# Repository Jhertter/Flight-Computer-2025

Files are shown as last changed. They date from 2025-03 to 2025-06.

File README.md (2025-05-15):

# ITBA Rocketry Team - Avionics&recovery
Documentation of SRAD Flight Computer

---

## Description

- Hardware design and implementation of the 2025 on board flight computer.
- Software used to capture data and transmit it to the ground station.

## FC implementation diagram

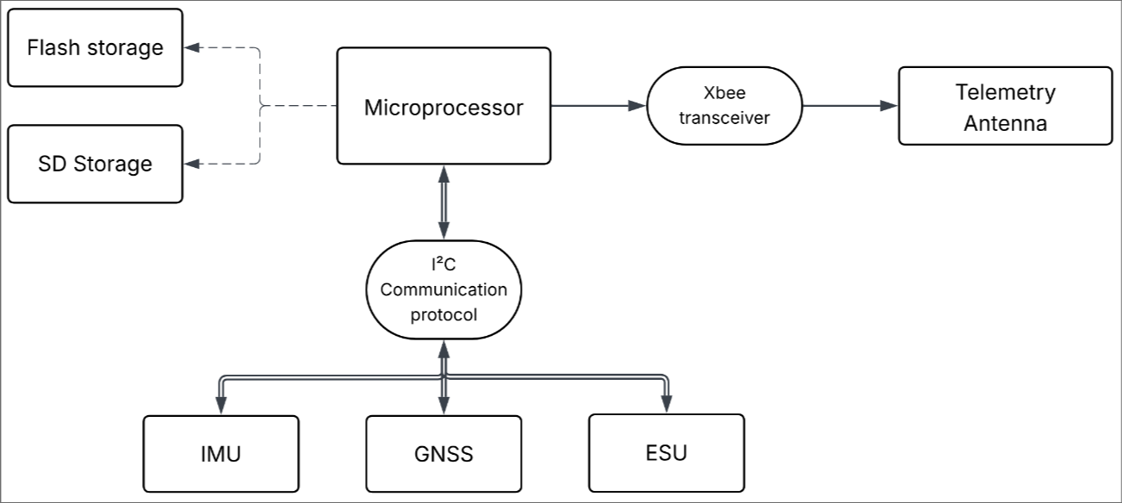
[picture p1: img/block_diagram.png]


## Authors

José Ivan Hertter
Ezequiel Diaz Guzmán

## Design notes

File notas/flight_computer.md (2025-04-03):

# ITBA Rocketry - A&Rocketry
## Flight Computer

### <u>Edición 2025</u>

Si llega a haber freno de aire, va a tener una cpu distinta

La placa SRAD tranquilamente puede ser de 90x150mm (el 90 está muy justo, el otro se puede ajustar). Si la tenemos lista para finales de febrero podriamos mandar a fabricarla.

Tener BOM para 28/01. Armar un GANT con final el 10/04

### Minutas reuniones

#### 10/03

2 compu/altimetros ccomercciales (RRC3 ni idea) 

ver si podemos activar la SRAD FC a mas de 2km o ver si se puede mantener prendido 10hs. Cambiaron el sensor de presion y temperatura

MPU 9050

puertos
RP4020 x3
flash x2
M8Q x1
bateria holder
18450  x4

Consideraciones de la placa
- dejar marcas de tornillos y bulones
- equilibrar la placa
- 90x120mm, puede ser hasta 150mm
- no poner todo de un lado y dejar el resto vacio
  
Investigar un poco sobre la placa para BMS

#### 27/03

- ~~usar shielding de GND para nets sensibles (SAM + flash)~~
- ver alternativas de capacitores para no usar 7 para la rpi -> miguel o pañol
- poner leds (pueden ser smd, mejor de colores distintos)
- ~~si es doble capa se puede usar nets como caps para VCC~~
- ~~conexión a xbee~~
- ~~poner opción de conectar una bornera y que un PMOS haga de llave driveado por el micro (camara), usa latch~~?
- ~~el MPU viene con placa integrada, es mejor sacarlo o dejarlo y conectar eso?~~
- poner pulsador por las dudas (ej: al tocar se envia la mem por el usb)
- no usar plano de masa general del otro lado (acople)
- ~~asegurarse que los caps de desacople esten antes de las entradas~~
- no exponer el BME280 a mucha luz (es fotosensible)
- a~~l gps va a haber que aisalrlo en la placa, dejarlo en una esquina separado y tiene que estar en un plano de GND de 50x50 mm ~~
- ~~ver SAM-M8Q Hardware Integration Manual, UBX-16018358 pag 12~~
- ~~usar conexión troncal para VCC y GND, dejar al final el gps~~
- va a haber que hacerle un case con tapa a la placa para evitar corrientes de aire
- usar pulsera antiestática
- a nivel bahía analizar la posición para maximizar el diagrama de radiación
- el regulador lo pondría arriba del usb, sería reg-usbc-jumper-bornera3

### Componentes

#### Micro
-   RP2040
    -   Cores: 2
    -   Clk: 133MHz
    -   GPIO: 34
    -   DAC: nada
    -   ADC: 4 canales, 12-bits
    -   Protocolos: UART, SPI, I2C, I2S, PIO    
    -   Consumo: es menor que el de Xtensa LX6
    -   Precio: ~$1000
    -   Comentarios: Como no vamos a usar los módulos wifi y bluetooth (las telemetrías se van a hacer por algún módulo LoRa), va a ser mejor usar el rp2040 para poder controlar mejor los modulos. Xtensa LX6 tiene limitaciones para operaciones en tiempo real (medio que ya lo vimos para el final de labo3). El RP2040 dicen que está diseñado especificamente para operaciones de baja latencia.
    -   PIO block: modulo para operaciones I/O de hasta 133MHz (en la esp llega a 40MHz masomenos)

#### Periféricos
- <u>Memoria:</u>
    - W25Q80DV:
        - Protocolo com: SPI
        - Precio: $477
-   <u>Sensor de presión:</u>
    -   BMP390. Podría usarse además un altimetro GPS para más precisión.
-   <u>GPS altimetro:</u>  
    -   GP-02
        -   Protocolo com: UART
        -   GNSS: BDS, GPS, GLONASS
        -   Precision: <2m
        -   Alimentacon: 3.3V
        -   Precio: $9600 + envio
    -   GlobalTop FGPMMOPA6H
    -   SparkFun GPS-RTK-SMA (ZED-F9P)
    -   u-blox NEO 8M:
        -   Protocolo com: UART, I²C, SPI
        -   GNSS: GPS, Galileo, BeiDou, GLONASS
        -   Precision: 1cm (RTK)
        -   Alimentación: 3.3V
        -   Precio: U$D 129
    -   Adafruit Ultimate GPS Module (MTK3339)
        -   Protocolo com: UART
- <u>Sensor de temperatura:</u>
    - HS3001: 
      - Protocolo com: I²C
      - Alimentación: 2.3V a 5.5V
      - Precisión: 0.25ºC
      - Rango: -10 a 80ºC
      - Precio: $3095
    - MAX31865
      - Protocolo com: 
      - Alimentación:
      - Precisión:
      - Rango: 
      - Precio: 
    - HTU21D      
      - Protocolo com: 
      - Alimentación:
      - Precisión:
      - Rango: 
      - Precio:
- <u>Acelerómetro y giroscopio:</u>
  - MPU6050:
      - Protocolo com:
      - Alimentación:
- <u>GPS:</u>

cargas pitorecnicas (despliegue nose cone y paracaidas)

### <u>Edición 2024</u>
#### Micro
-   ESP32 (Xtensa LX6):
    -   Cores: 2
    -   Clk: 240MHz
    -   GPIO: 34
    -   DAC: 2 canales, 8-bit
    -   ADC: 18 canales, 12-bits
    -   Protocolos: UART, SPI, I2C, I2S, CAN
    -   Precio: 
#### Perifericos
-   <u>Sensor de presión:</u> BMP390.
    -   Protocolo de com: I²C y SPI
    -   Precio unitario:
    -   Para medir altitud. Cons. Requiere calibración con la presión atmosférica del lugar y es muy sensible a cambios climaticos.
-   <u>Memoria:</u> W25Q80DV. 
    -   Serial flash memory. 
    -   Protocolo de com: SPI.
    -   Precio unitario: 
-   <u>Acelerometro:</u> MPU-6050. 
    -   Protocolo de com: I²C. *
    -   Precio unitario:
    -   Tiene giroscopio. 
-   <u>Pyro channels:</u>   
-   <u>Regulador de tensión:</u>
    -   Precio unitario: *

### 2023

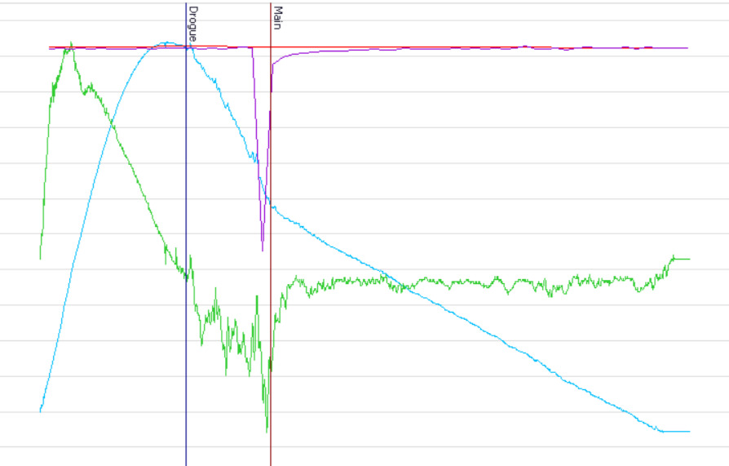
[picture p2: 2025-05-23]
2024_lanin_data/croped.jpg

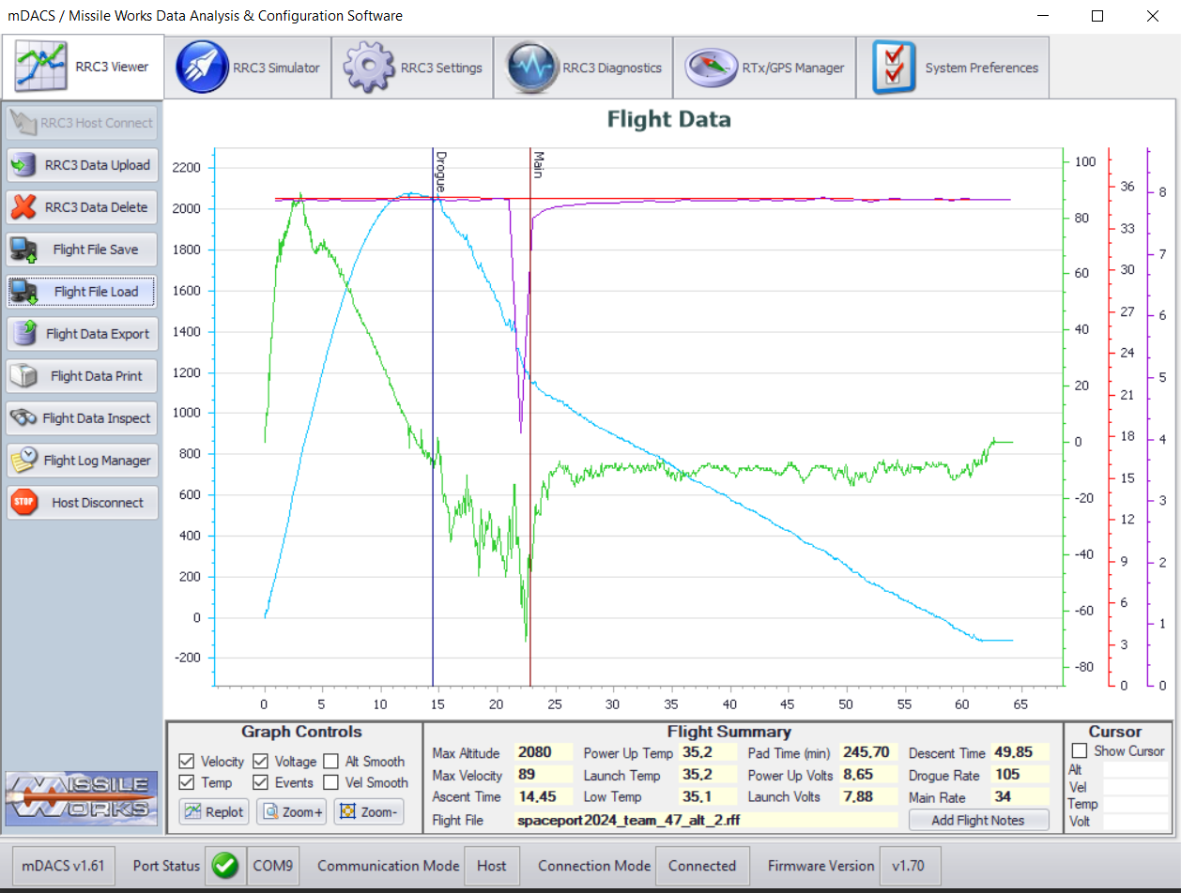
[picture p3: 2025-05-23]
2024_lanin_data/spaceport2024_team_47_alt_2.png

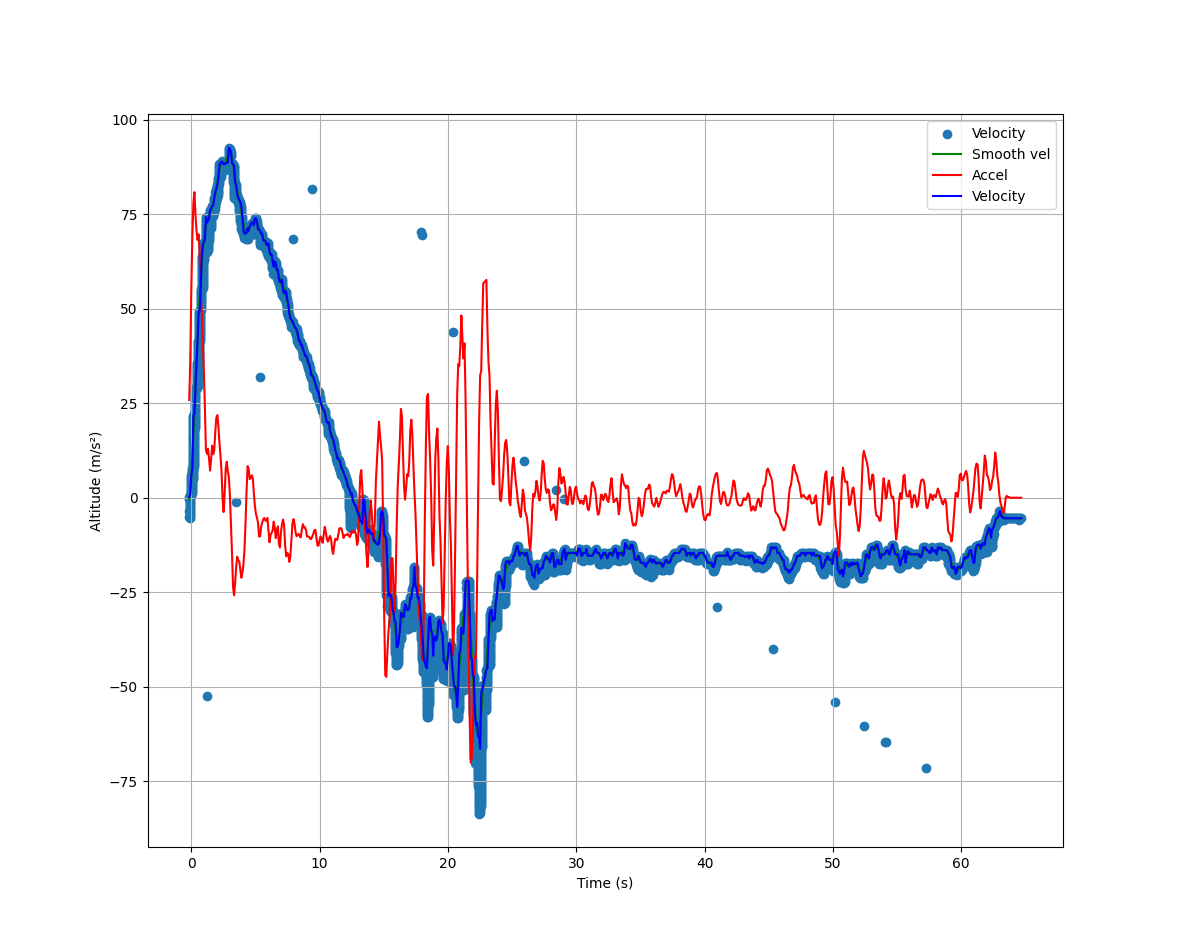
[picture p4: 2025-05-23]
2024_lanin_data/full_mission.png

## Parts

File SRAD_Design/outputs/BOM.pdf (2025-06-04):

BOM

Id Designator
14 U1
20 U2
6 J7
30 U3
17 R9
4 R2
15 R3,R4
26 R1,R5
5 R15,R16,R14
8 R13,R12
10 R_BME_SDA1,R_BME_SCL1,R_SAM_SDA1,R_MPU_SCL1,R_MPU_SDA1,R_SAM_SCL1 13 R_BL2
21 R10,R11
22 R_BL1
19 S2,S3,S1
28 U4
12 J5
18 J1
25 U5
32 U6
1 D2,D1,D3
9 Y1
3 C8,C10
7 C1,C4,C17
24 C6,C14,C13,C15,C7,C11,C12,C9,C5,C16
29 C2,C3
2 C_BME_VDDIO1,C_VDD_MPU1,C_MPU_REG1,C_BME_VDD1 11 C_VDDIO_MPU1
16 C_SAM_VCCIO1,C_SAM_VCC1,C_SAM_VBCKP1
23 C18
27 J4
31 J2

Footprint | Quantity Designation
SOT-223-3_TabPin2 | 1 NCP1117-3.3_SOT223
SOIC-8_5.3x5.3mm_P1.27mm | 1 W25Q128JVS
SAMESKY_UJ20-C-H-G-SMT-6-P16-TR | 1 UJ20-C-H-G-SMT-6-P16-TR
RP2040-QFN-56 | 1 RP2040
R_0805_2012Metric_Pad1.20x1.40mm_HandSolder | 1 | 150
R_0805_2012Metric | 1 DNF
R_0805_2012Metric | 2 | 27
R_0805_2012Metric | 2 1k
R_0805 | 3 10k
R_0805 | 2 R
R_0805 | 6 2k7
R_0805 | 1 8k2
R_0805 | 2 | 150
R_0805 | 1 15k
PTS810SJK250SMTRLFS | 3 PTS810SJK250SMTR_LFS
PSON65P250X250X100-8N | 1 BME280
PinHeader_1x03_P2.54mm_Vertical | 1 Connector_3_Pol
PinHeader_1x02_P2.54mm_Vertical | 1 Connector_2_Pol
MPU-9250 | 1 MPU-9250
MODULE_SAM-M8Q-0-10 | 1 SAM-M8Q-0-10
LED_0805_2012Metric_Pad1.15x1.40mm_HandSolder | 3 LED
Crystal_HC49-4H_Vertical | 1 Crystal
C_0805_2012Metric | 2 1u
C_0805_2012Metric | 3 10u
C_0805_2012Metric | 10 100n
C_0805_2012Metric | 2 15p
C_0805 | 4 100n
C_0805 | 1 10n
C_0805 | 3 C
C_0805 | 1 10u
Bornera_2_P5mm | 1 Terminal_2
693071010811 | 1 503398-1892

Supplier and ref

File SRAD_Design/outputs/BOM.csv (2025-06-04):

Id | Designator | Footprint | Quantity | Designation | Supplier and ref
1 | D2,D1,D3 | LED_0805_2012Metric_Pad1.15x1.40mm_HandSolder | 3 | LED
2 | C_BME_VDDIO1,C_VDD_MPU1,C_MPU_REG1,C_BME_VDD1 | C_0805 | 4 | 100n
3 | C8,C10 | C_0805_2012Metric | 2 | 1u
4 | R2 | R_0805_2012Metric | 1 | DNF
5 | R15,R16,R14 | R_0805 | 3 | 10k
6 | J7 | SAMESKY_UJ20-C-H-G-SMT-6-P16-TR | 1 | UJ20-C-H-G-SMT-6-P16-TR
7 | C1,C4,C17 | C_0805_2012Metric | 3 | 10u
8 | R13,R12 | R_0805 | 2 | R
9 | Y1 | Crystal_HC49-4H_Vertical | 1 | Crystal
10 | R_BME_SDA1,R_BME_SCL1,R_SAM_SDA1,R_MPU_SCL1,R_MPU_SDA1,R_SAM_SCL1 | R_0805 | 6 | 2k7
11 | C_VDDIO_MPU1 | C_0805 | 1 | 10n
12 | J5 | PinHeader_1x03_P2.54mm_Vertical | 1 | Connector_3_Pol
13 | R_BL2 | R_0805 | 1 | 8k2
14 | U1 | SOT-223-3_TabPin2 | 1 | NCP1117-3.3_SOT223
15 | R3,R4 | R_0805_2012Metric | 2 | 27
16 | C_SAM_VCCIO1,C_SAM_VCC1,C_SAM_VBCKP1 | C_0805 | 3 | C
17 | R9 | R_0805_2012Metric_Pad1.20x1.40mm_HandSolder | 1 | 150
18 | J1 | PinHeader_1x02_P2.54mm_Vertical | 1 | Connector_2_Pol
19 | S2,S3,S1 | PTS810SJK250SMTRLFS | 3 | PTS810SJK250SMTR_LFS
20 | U2 | SOIC-8_5.3x5.3mm_P1.27mm | 1 | W25Q128JVS
21 | R10,R11 | R_0805 | 2 | 150
22 | R_BL1 | R_0805 | 1 | 15k
23 | C18 | C_0805 | 1 | 10u
24 | C6,C14,C13,C15,C7,C11,C12,C9,C5,C16 | C_0805_2012Metric | 10 | 100n
25 | U5 | MPU-9250 | 1 | MPU-9250
26 | R1,R5 | R_0805_2012Metric | 2 | 1k
27 | J4 | Bornera_2_P5mm | 1 | Terminal_2
28 | U4 | PSON65P250X250X100-8N | 1 | BME280
29 | C2,C3 | C_0805_2012Metric | 2 | 15p
30 | U3 | RP2040-QFN-56 | 1 | RP2040
31 | J2 | 693071010811 | 1 | 503398-1892
32 | U6 | MODULE_SAM-M8Q-0-10 | 1 | SAM-M8Q-0-10

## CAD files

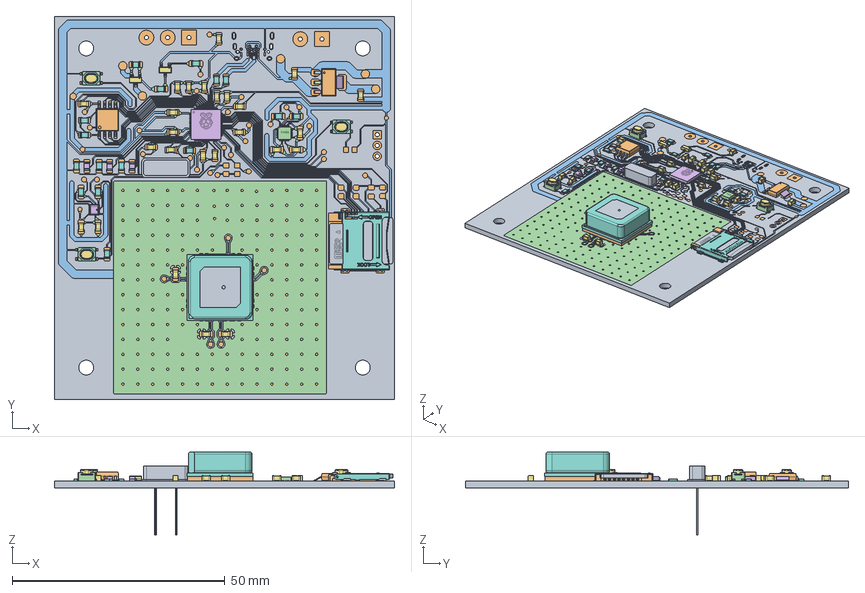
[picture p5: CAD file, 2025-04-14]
SRAD_Design/SRAD_computer.FCStd
80.0 x 90.0 x 19.5 mm
Pcb_98ea
topPads_98ea
topTracks_98ea
topZones_98ea
botPads_98ea
D2_LED_0805_2012Metric_d771bca645d1 x 3
C_BME_VDDIO1_C_0805_2012Metric_c2abb37d300b x 25
R7_R_0805_2012Metric_f4d0965d4664 x 16
Y1_ECS-120-20-4_43d50dad4b6c
PinsArrayL
PinsArrayL001
PinsArrayL002
FilletPinR
PinsArrayL004 x 2
PinsArrayL005 x 2
FilletPinR001 x 2
PTS810SJK250SMTR LFS x 3
PTS810SJK250SMTR LFS001 x 3
PTS810SJK250SMTR LFS002 x 3
PTS810SJK250SMTR LFS003 x 3
PTS810SJK250SMTR LFS004 x 3
PTS810SJK250SMTR LFS005 x 3
PTS810SJK250SMTR LFS006 x 3
MICRO SD CARD
PinsArrayLR
PinsArrayLR001
PinsArrayLR002
PinsArrayLR003
PinsArrayLR004
PinsArrayLR005
PinsArrayLR006
PinsArrayLR007
ICM-20948
ICM-20949
ICM-20950
ICM-20951
ICM-20952
ICM-20953
ICM-20954
ICM-20955
ICM-20956
ICM-20957
ICM-20958
ICM-20959
ICM-20960
ICM-20961
ICM-20962
ICM-20963
ICM-20964
ICM-20965
ICM-20966
ICM-20967
ICM-20968
ICM-20969
ICM-20970
ICM-20971
ICM-20972
ICM-20973
BME280
BME281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

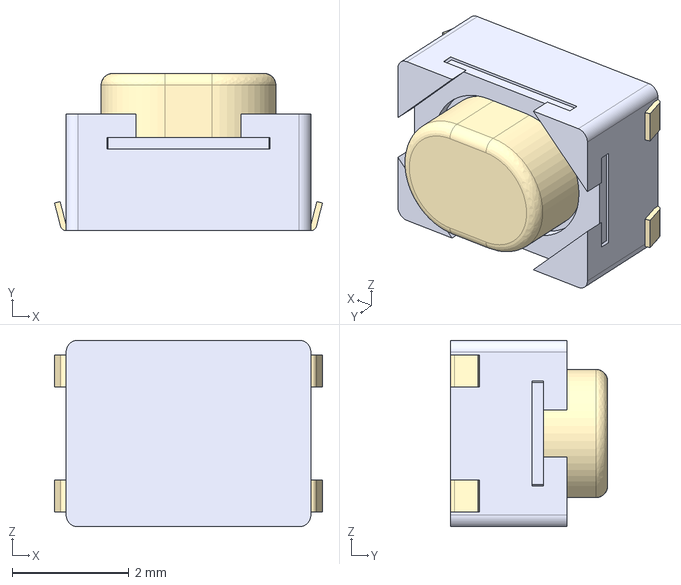
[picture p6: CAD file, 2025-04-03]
SRAD_Design/3dmodels/PTS810SJK250SMTR_LFS.step
4.60 x 2.70 x 3.20 mm

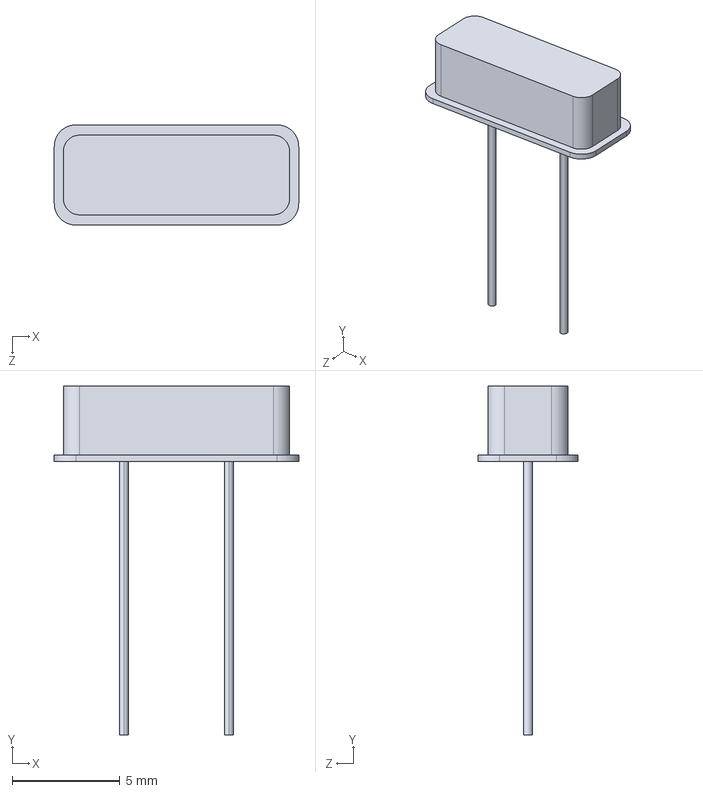
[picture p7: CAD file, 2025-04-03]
SRAD_Design/3dmodels/Crystal_HC49-4H.step
11.3 x 16.2 x 4.65 mm

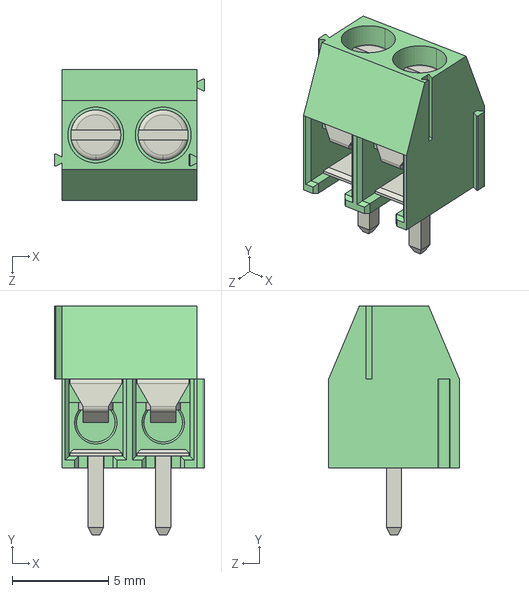
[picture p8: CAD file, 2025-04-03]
SRAD_Design/3dmodels/Terminal_Block_2.step
7.80 x 11.9 x 6.80 mm

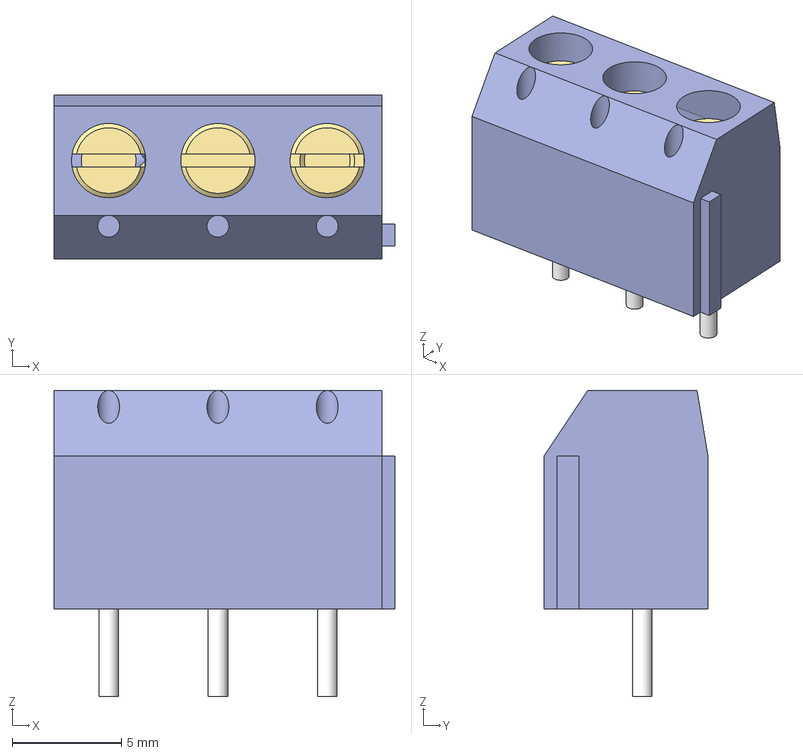
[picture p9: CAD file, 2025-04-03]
SRAD_Design/3dmodels/Terminal_Block_3.step
15.6 x 7.50 x 14.0 mm

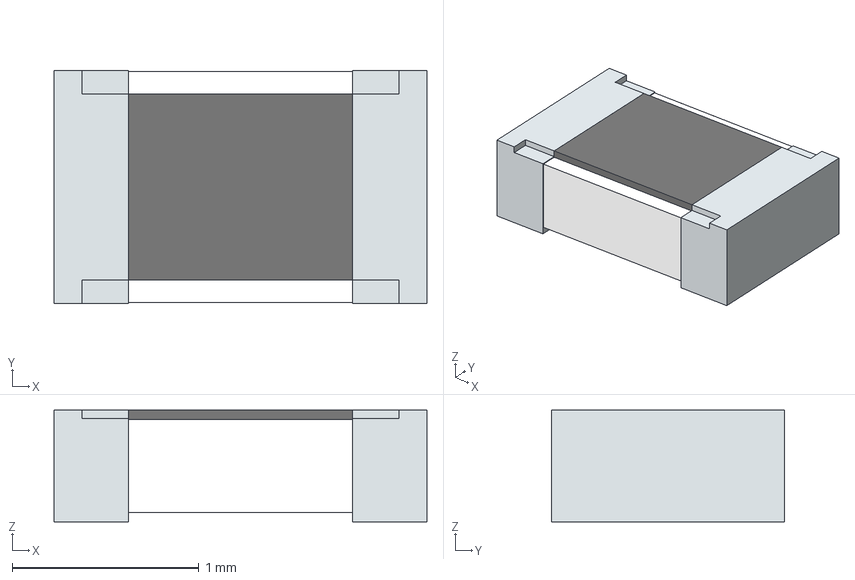
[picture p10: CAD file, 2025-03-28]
SRAD_Design/3dmodels/0805_res.step
2.00 x 1.25 x 0.6 mm
solidBody
Terminal
solidTop

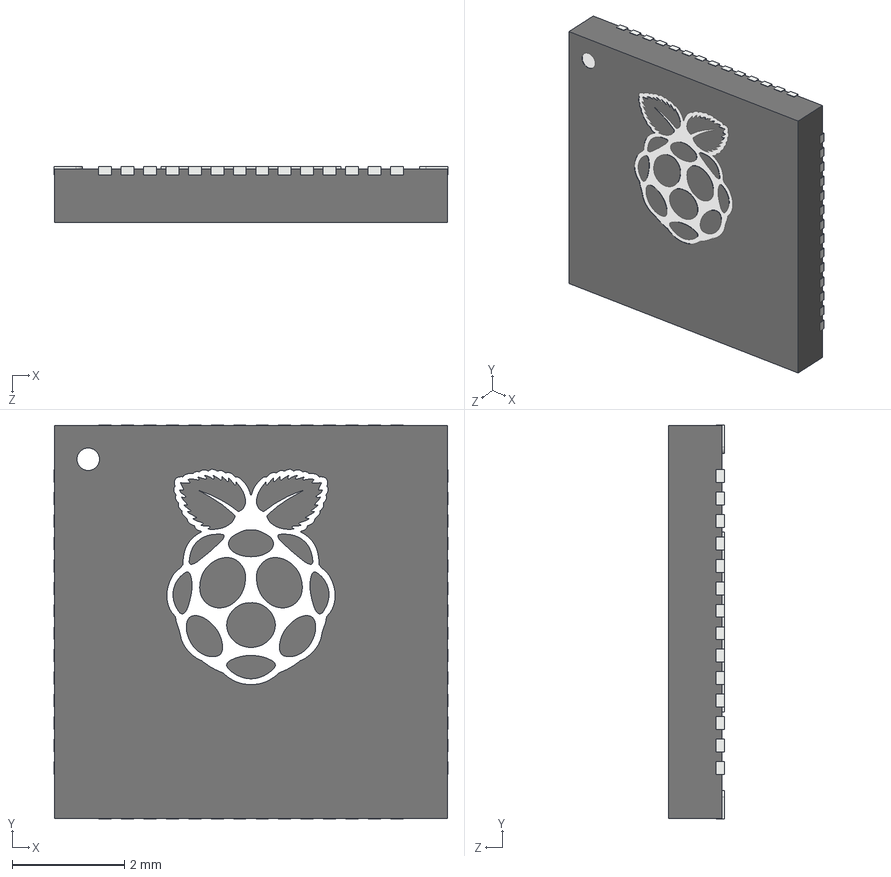
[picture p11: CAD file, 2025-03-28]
SRAD_Design/3dmodels/RP2040_QFN_PACKAGE.STEP
7.02 x 7.02 x 1.00 mm

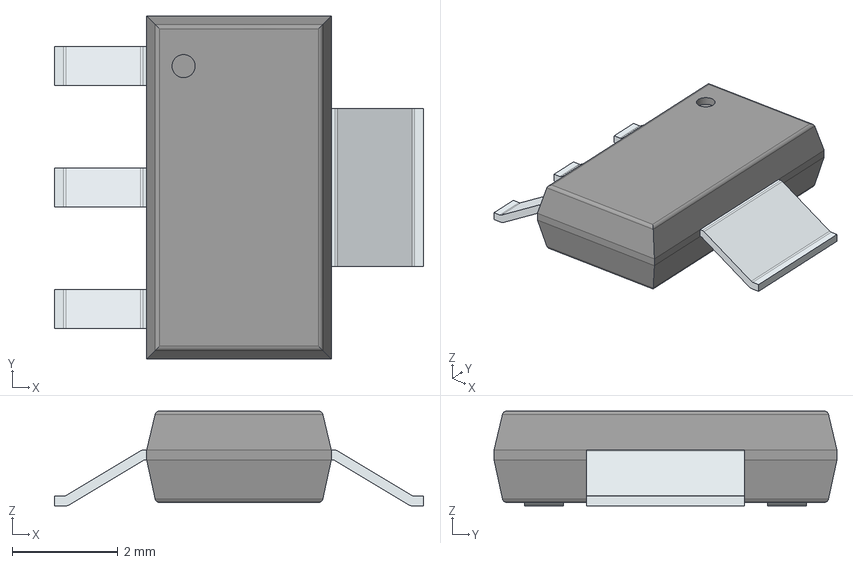
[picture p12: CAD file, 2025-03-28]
SRAD_Design/3dmodels/sot223.step
7.00 x 6.50 x 1.80 mm
PinsArrayL
FilletPinR

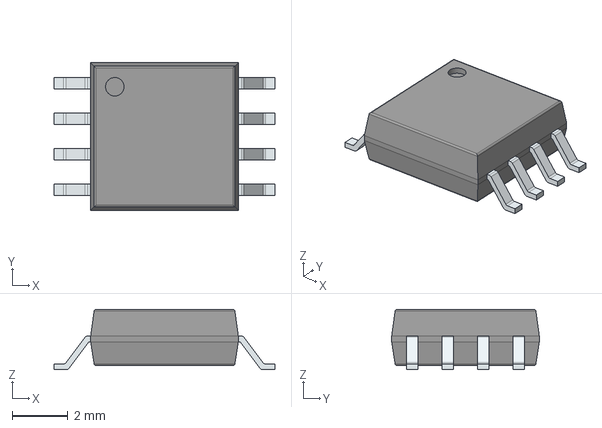
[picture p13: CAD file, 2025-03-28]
SRAD_Design/3dmodels/W25Q128JVSIM.step
7.90 x 5.28 x 2.16 mm
PinsArrayLR

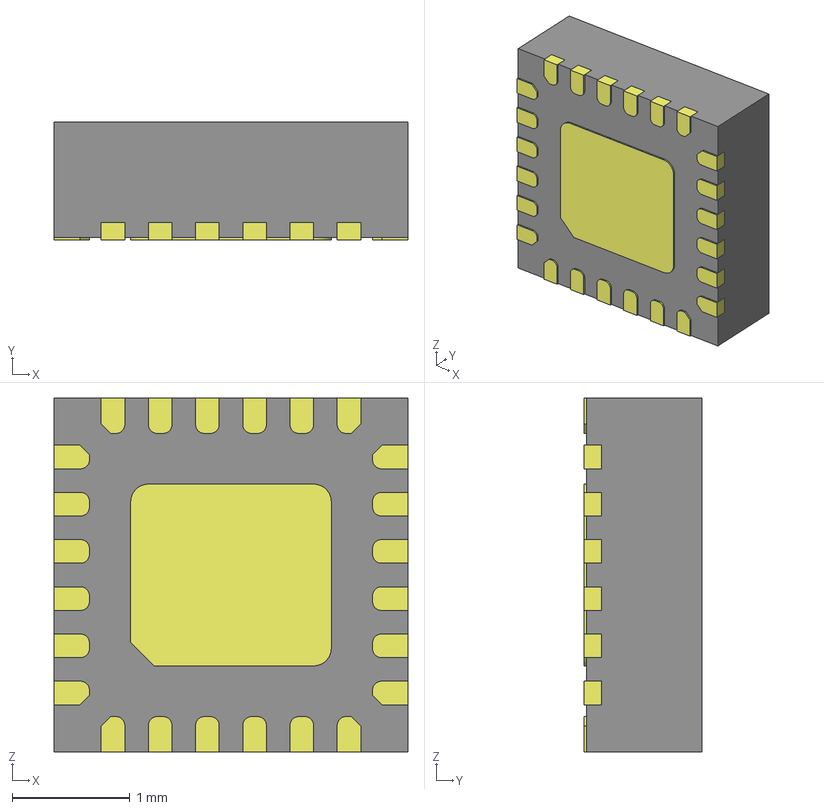
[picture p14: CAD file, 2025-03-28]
SRAD_Design/3dmodels/MPU-9250.step
3.00 x 1.00 x 3.00 mm

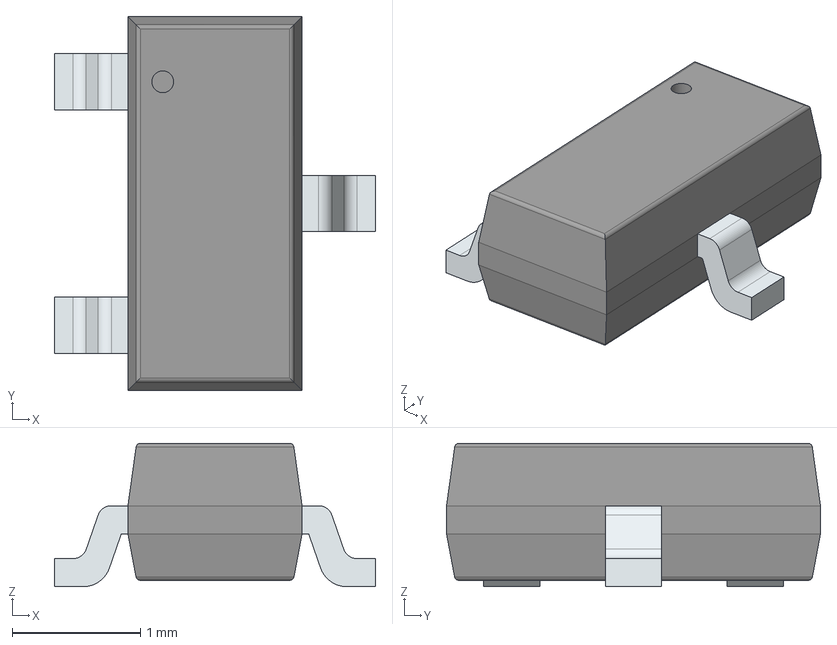
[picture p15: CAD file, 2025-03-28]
SRAD_Design/3dmodels/sot23_3.step
2.51 x 2.92 x 1.12 mm
PinsArrayL
FilletPinR

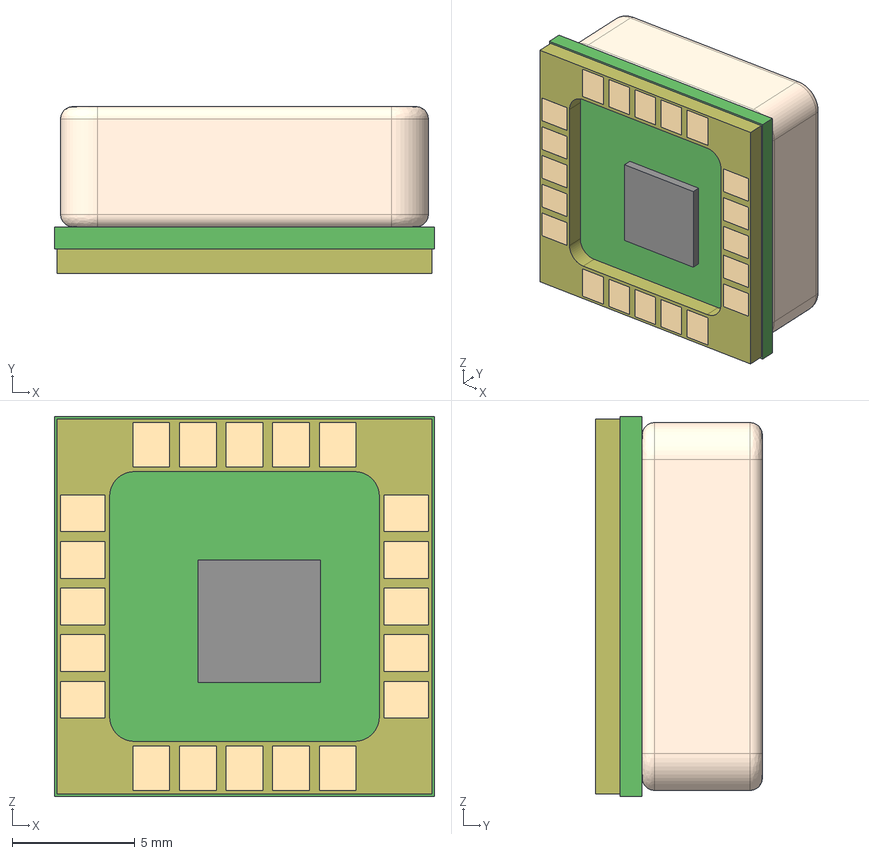
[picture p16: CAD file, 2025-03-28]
SRAD_Design/3dmodels/SAM-M8Q-0.step
15.5 x 6.80 x 15.5 mm
SAM-M8Q-0-10_22
SAM-M8Q-0-10_14
SAM-M8Q-0-10_24
SAM-M8Q-0-10_13
SAM-M8Q-0-10_11
SAM-M8Q-0-10_16
SAM-M8Q-0-10_20
SAM-M8Q-0-10_3
SAM-M8Q-0-10_25
SAM-M8Q-0-10_5
SAM-M8Q-0-10_21
SAM-M8Q-0-10_12
SAM-M8Q-0-10_9
SAM-M8Q-0-10_8
SAM-M8Q-0-10_10
SAM-M8Q-0-10_15
SAM-M8Q-0-10_2
SAM-M8Q-0-10_7
SAM-M8Q-0-10
SAM-M8Q-0-10_6
SAM-M8Q-0-10_1
SAM-M8Q-0-10_18
SAM-M8Q-0-10_17
SAM-M8Q-0-10_23
SAM-M8Q-0-10_4
SAM-M8Q-0-10_19

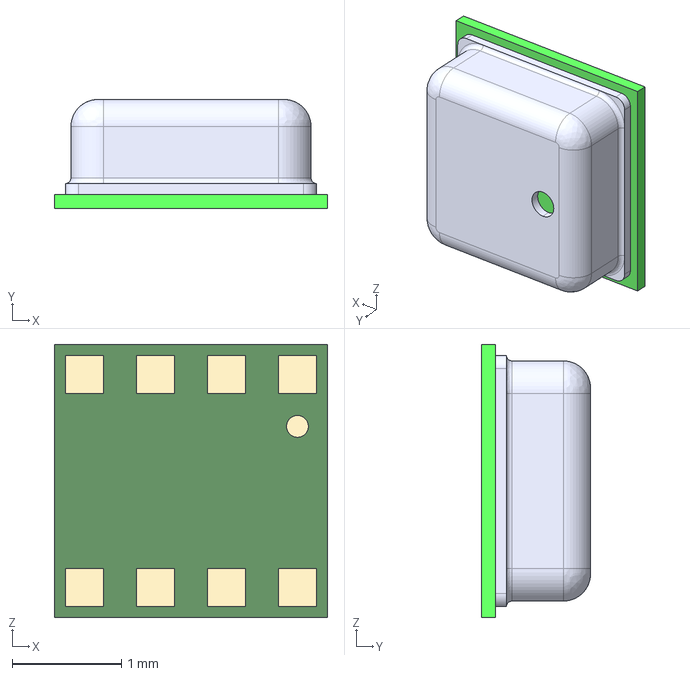
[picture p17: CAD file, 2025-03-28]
SRAD_Design/3dmodels/BME280.step
2.50 x 1.00 x 2.50 mm

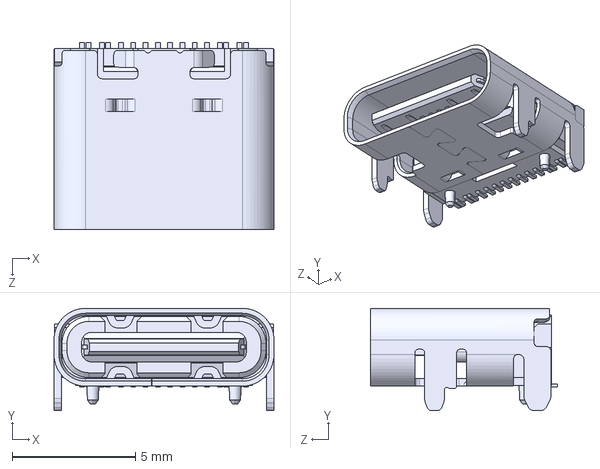
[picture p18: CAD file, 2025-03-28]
SRAD_Design/3dmodels/Same_Sky_UJ20-C-H-G-SMT-1-P16-TR.step
8.94 x 4.16 x 7.60 mm

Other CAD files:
SRAD_Design/3dmodels/503398-1892.step

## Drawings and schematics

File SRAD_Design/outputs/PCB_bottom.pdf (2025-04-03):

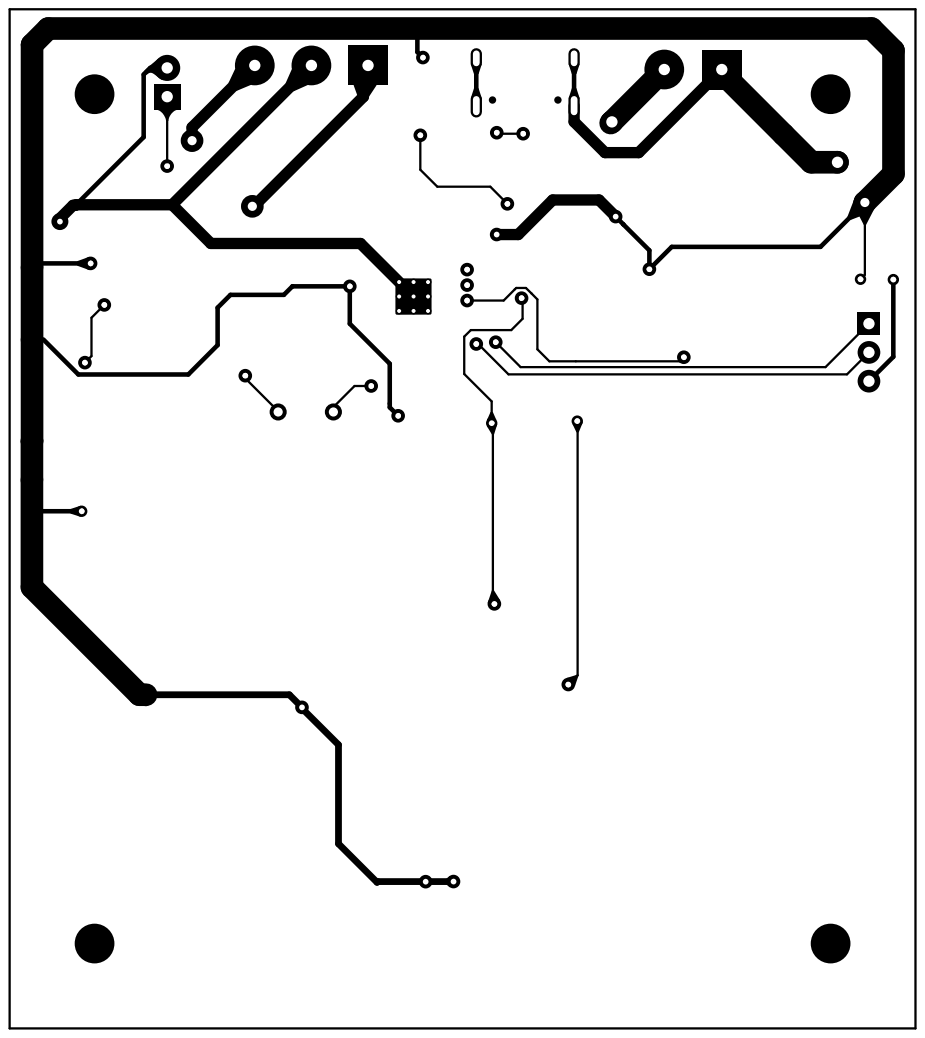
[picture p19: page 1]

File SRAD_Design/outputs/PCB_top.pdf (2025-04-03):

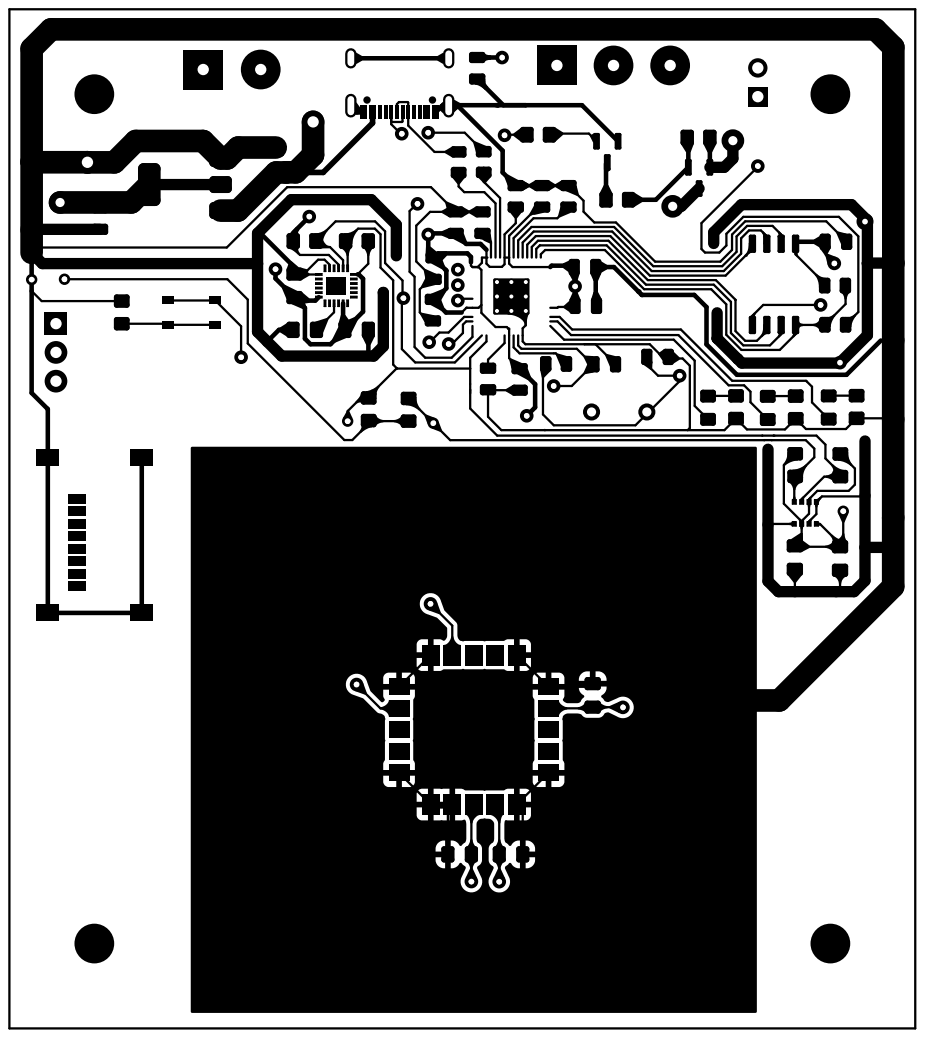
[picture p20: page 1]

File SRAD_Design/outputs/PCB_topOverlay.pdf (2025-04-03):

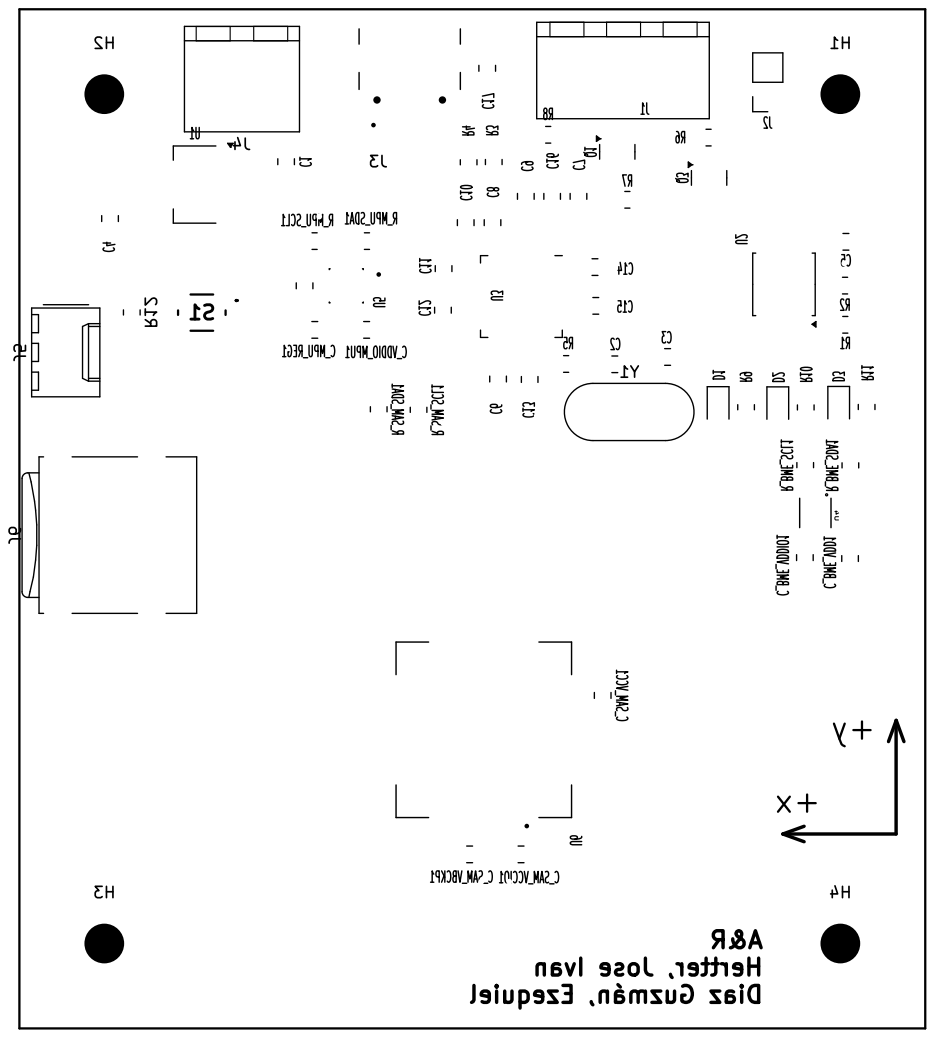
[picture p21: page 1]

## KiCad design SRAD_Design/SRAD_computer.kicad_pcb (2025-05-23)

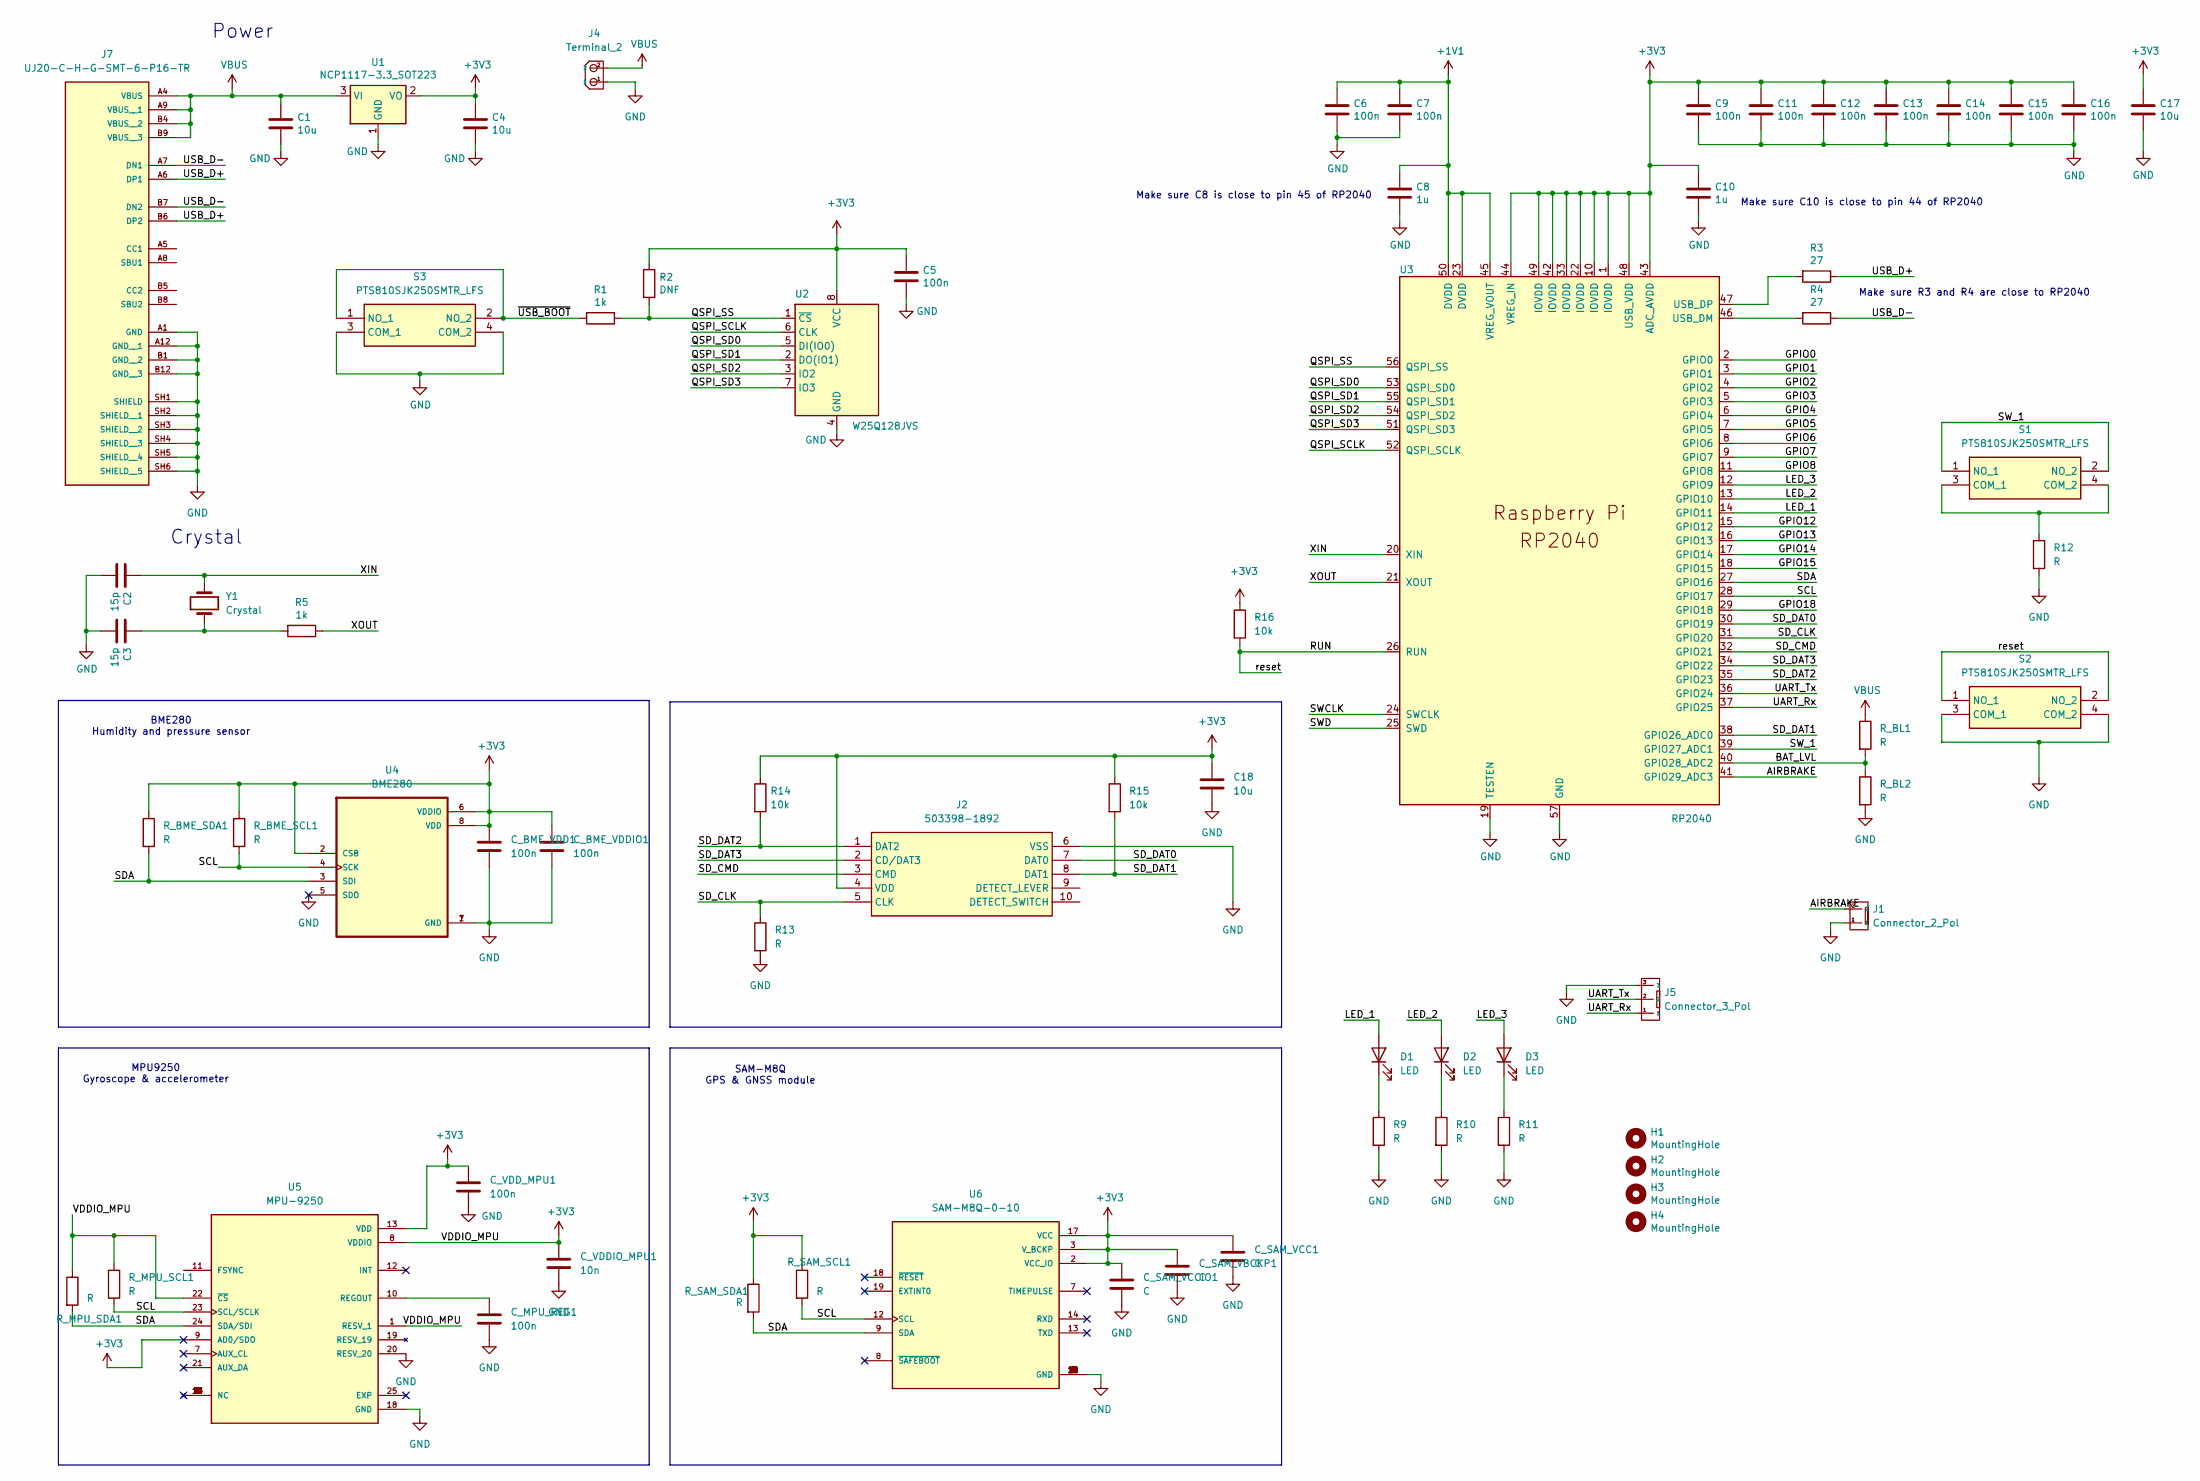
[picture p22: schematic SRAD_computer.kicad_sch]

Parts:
C1, C4, C17: 10u; C_0805_2012Metric
C2, C3: 15p; C_0805_2012Metric
C5, C6, C7, C9, C11, C12, C13, C14, C15, C16: 100n; C_0805_2012Metric
C8, C10: 1u; C_0805_2012Metric
C18: 10u; C_0805
C_BME_VDD1: 100n; C_0805
C_BME_VDDIO1: 100n; C_0805
C_MPU_REG1: 100n; C_0805
C_SAM_VBCKP1: C; C_0805
C_SAM_VCC1: C; C_0805
C_SAM_VCCIO1: C; C_0805
C_VDDIO_MPU1: 10n; C_0805
C_VDD_MPU1: 100n; C_0805
D1, D2, D3: LED; LED_0805_2012Metric_Pad1.15x1.40mm_HandSolder
H1, H2, H3, H4: MountingHole; MountingHole_3.5mm
J1: Connector_2_Pol; PinHeader_1x02_P2.54mm_Vertical
J2: 503398-1892; 693071010811; Mouser Part Number 538-503398-1892
J4: Terminal_2; Bornera_2_P5mm
J5: Connector_3_Pol; PinHeader_1x03_P2.54mm_Vertical
J7: UJ20-C-H-G-SMT-6-P16-TR; SAMESKY_UJ20-C-H-G-SMT-6-P16-TR; PARTREV 1.01
R1, R5: 1k; R_0805_2012Metric
R2: DNF; R_0805_2012Metric
R3, R4: 27; R_0805_2012Metric
R9: R; R_0805_2012Metric_Pad1.20x1.40mm_HandSolder
R10, R11, R12, R13: R; R_0805
R14, R15, R16: 10k; R_0805
R_BL1, R_BL2: R; R_0805
R_BME_SCL1: R; R_0805
R_BME_SDA1: R; R_0805
R_MPU_SCL1: R; R_0805
R_MPU_SDA1: R; R_0805
R_SAM_SCL1: R; R_0805
R_SAM_SDA1: R; R_0805
S1, S2, S3: PTS810SJK250SMTR_LFS; PTS810SJK250SMTRLFS; Mouser Part Number 611-PTS810SJK250SMTR
U1: NCP1117-3.3_SOT223; SOT-223-3_TabPin2
U2: W25Q128JVS; SOIC-8_5.3x5.3mm_P1.27mm
U3: RP2040; RP2040-QFN-56
U4: BME280; PSON65P250X250X100-8N
U5: MPU-9250; PARTREV 1.1
U6: SAM-M8Q-0-10; MODULE_SAM-M8Q-0-10; PARTREV R07
Y1: Crystal; Crystal_HC49-4H_Vertical

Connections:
+1V1: C6.1, C7.1, C8.1, U3.23 (DVDD), U3.45 (VREG_VOUT), U3.50 (DVDD)
+3V3: C4.1, C5.1, C9.1, C10.1, C11.1, C12.1, C13.1, C14.1, C15.1, C16.1, C17.1, C18.1, C_BME_VDD1.1, C_BME_VDDIO1.1, C_SAM_VBCKP1.1, C_SAM_VCC1.1, C_SAM_VCCIO1.1, C_VDDIO_MPU1.1, C_VDD_MPU1.1, J2.4 (VDD), R2.1, R14.1, R15.1, R16.1, R_BME_SCL1.1, R_BME_SDA1.1, R_MPU_SCL1.1, R_MPU_SDA1.1, R_SAM_SCL1.1, R_SAM_SDA1.1, U1.2 (VO), U2.8 (VCC), U3.1 (IOVDD), U3.10 (IOVDD), U3.22 (IOVDD), U3.33 (IOVDD), U3.42 (IOVDD), U3.43 (ADC_AVDD), U3.44 (VREG_IN), U3.48 (USB_VDD), U3.49 (IOVDD), U4.2 (CSB), U4.6 (VDDIO), U4.8 (VDD), U5.1 (RESV_1), U5.8 (VDDIO), U5.9 (AD0/SDO), U5.13 (VDD), U5.22 (~CS), U6.2 (VCC_IO), U6.3 (V_BCKP), U6.17 (VCC)
/AIRBRAKE: J1.2, U3.41 (GPIO29_ADC3)
/BAT_LVL: R_BL1.2, R_BL2.1, U3.40 (GPIO28_ADC2)
/GPIO0: U3.2 (GPIO0)
/GPIO1: U3.3 (GPIO1)
/GPIO2: U3.4 (GPIO2)
/GPIO3: U3.5 (GPIO3)
/GPIO4: U3.6 (GPIO4)
/GPIO5: U3.7 (GPIO5)
/GPIO6: U3.8 (GPIO6)
/GPIO7: U3.9 (GPIO7)
/GPIO8: U3.11 (GPIO8)
/GPIO12: U3.15 (GPIO12)
/GPIO13: U3.16 (GPIO13)
/GPIO14: U3.17 (GPIO14)
/GPIO15: U3.18 (GPIO15)
/GPIO18: U3.29 (GPIO18)
/LED_1: D1.2 (A), U3.14 (GPIO11)
/LED_2: D2.2 (A), U3.13 (GPIO10)
/LED_3: D3.2 (A), U3.12 (GPIO9)
/QSPI_SCLK: U2.6 (CLK), U3.52 (QSPI_SCLK)
/QSPI_SD0: U2.5 (DI(IO0)), U3.53 (QSPI_SD0)
/QSPI_SD1: U2.2 (DO(IO1)), U3.55 (QSPI_SD1)
/QSPI_SD2: U2.3 (IO2), U3.54 (QSPI_SD2)
/QSPI_SD3: U2.7 (IO3), U3.51 (QSPI_SD3)
/QSPI_SS: R1.1, R2.2, U2.1 (~CS), U3.56 (QSPI_SS)
/RUN: R16.2, S2.1 (NO_1), S2.2 (NO_2), U3.26 (RUN)
/SCL: R_BME_SCL1.2, R_MPU_SCL1.2, R_SAM_SCL1.2, U3.28 (GPIO17), U4.4 (SCK), U5.23 (SCL/SCLK), U6.12 (SCL)
/SDA: R_BME_SDA1.2, R_MPU_SDA1.2, R_SAM_SDA1.2, U3.27 (GPIO16), U4.3 (SDI), U5.24 (SDA/SDI), U6.9 (SDA)
/SD_CLK: J2.5 (CLK), R13.1, U3.31 (GPIO20)
/SD_CMD: J2.3 (CMD), U3.32 (GPIO21)
/SD_DAT0: J2.7 (DAT0), U3.30 (GPIO19)
/SD_DAT1: J2.8 (DAT1), R15.2, U3.38 (GPIO26_ADC0)
/SD_DAT2: J2.1 (DAT2), R14.2, U3.35 (GPIO23)
/SD_DAT3: J2.2 (CD/DAT3), U3.34 (GPIO22)
/SWCLK: U3.24 (SWCLK)
/SWD: U3.25 (SWD)
/SW_1: S1.1 (NO_1), S1.2 (NO_2), U3.39 (GPIO27_ADC1)
/UART_Rx: J5.1, U3.37 (GPIO25)
/UART_Tx: J5.2, U3.36 (GPIO24)
/USB_D+: J7.A6 (DP1), J7.B6 (DP2), R3.1
/USB_D-: J7.A7 (DN1), J7.B7 (DN2), R4.1
/XIN: C2.1, U3.20 (XIN), Y1.2
/XOUT: R5.1, U3.21 (XOUT)
/~USB_BOOT: R1.2, S3.1 (NO_1), S3.2 (NO_2)
GND: C1.2, C2.2, C3.2, C4.2, C5.2, C6.2, C7.2, C8.2, C9.2, C10.2, C11.2, C12.2, C13.2, C14.2, C15.2, C16.2, C17.2, C18.2, C_BME_VDD1.2, C_BME_VDDIO1.2, C_MPU_REG1.2, C_SAM_VBCKP1.2, C_SAM_VCC1.2, C_SAM_VCCIO1.2, C_VDDIO_MPU1.2, C_VDD_MPU1.2, J1.1, J2.6 (VSS), J4.1, J5.3, J7.A1 (GND), J7.A12 (GND__1), J7.B1 (GND__2), J7.B12 (GND__3), J7.SH1 (SHIELD), J7.SH2 (SHIELD__1), J7.SH3 (SHIELD__2), J7.SH4 (SHIELD__3), J7.SH5 (SHIELD__4), J7.SH6 (SHIELD__5), R9.2, R10.2, R11.2, R12.2, R13.2, R_BL2.2, S2.3 (COM_1), S2.4 (COM_2), S3.3 (COM_1), S3.4 (COM_2), U1.1 (GND), U2.4 (GND), U3.19 (TESTEN), U3.57 (GND), U4.1 (GND), U4.5 (SDO), U4.7 (GND), U5.18 (GND), U5.20 (RESV_20), U6.1 (GND), U6.4 (GND), U6.5 (GND), U6.6 (GND), U6.10 (GND), U6.11 (GND), U6.15 (GND), U6.16 (GND), U6.20 (GND)
unnamed: C3.1, R5.2, Y1.1
unnamed: D1.1 (K), R9.1
unnamed: D2.1 (K), R10.1
unnamed: D3.1 (K), R11.1
unnamed: R12.1, S1.3 (COM_1), S1.4 (COM_2)
unnamed: R4.2, U3.46 (USB_DM)
unnamed: R3.2, U3.47 (USB_DP)
unnamed: C_MPU_REG1.1, U5.10 (REGOUT)
VBUS: C1.1, J4.2, J7.A4 (VBUS), J7.A9 (VBUS__1), J7.B4 (VBUS__2), J7.B9 (VBUS__3), R_BL1.1, U1.3 (VI)

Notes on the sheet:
SAM-M8Q GPS & GNSS module
Crystal
Make sure C10 is close to pin 44 of RP2040
Make sure R3 and R4 are close to RP2040
BME280 Humidity and pressure sensor
MPU9250 Gyroscope & accelerometer
Power
Make sure C8 is close to pin 45 of RP2040

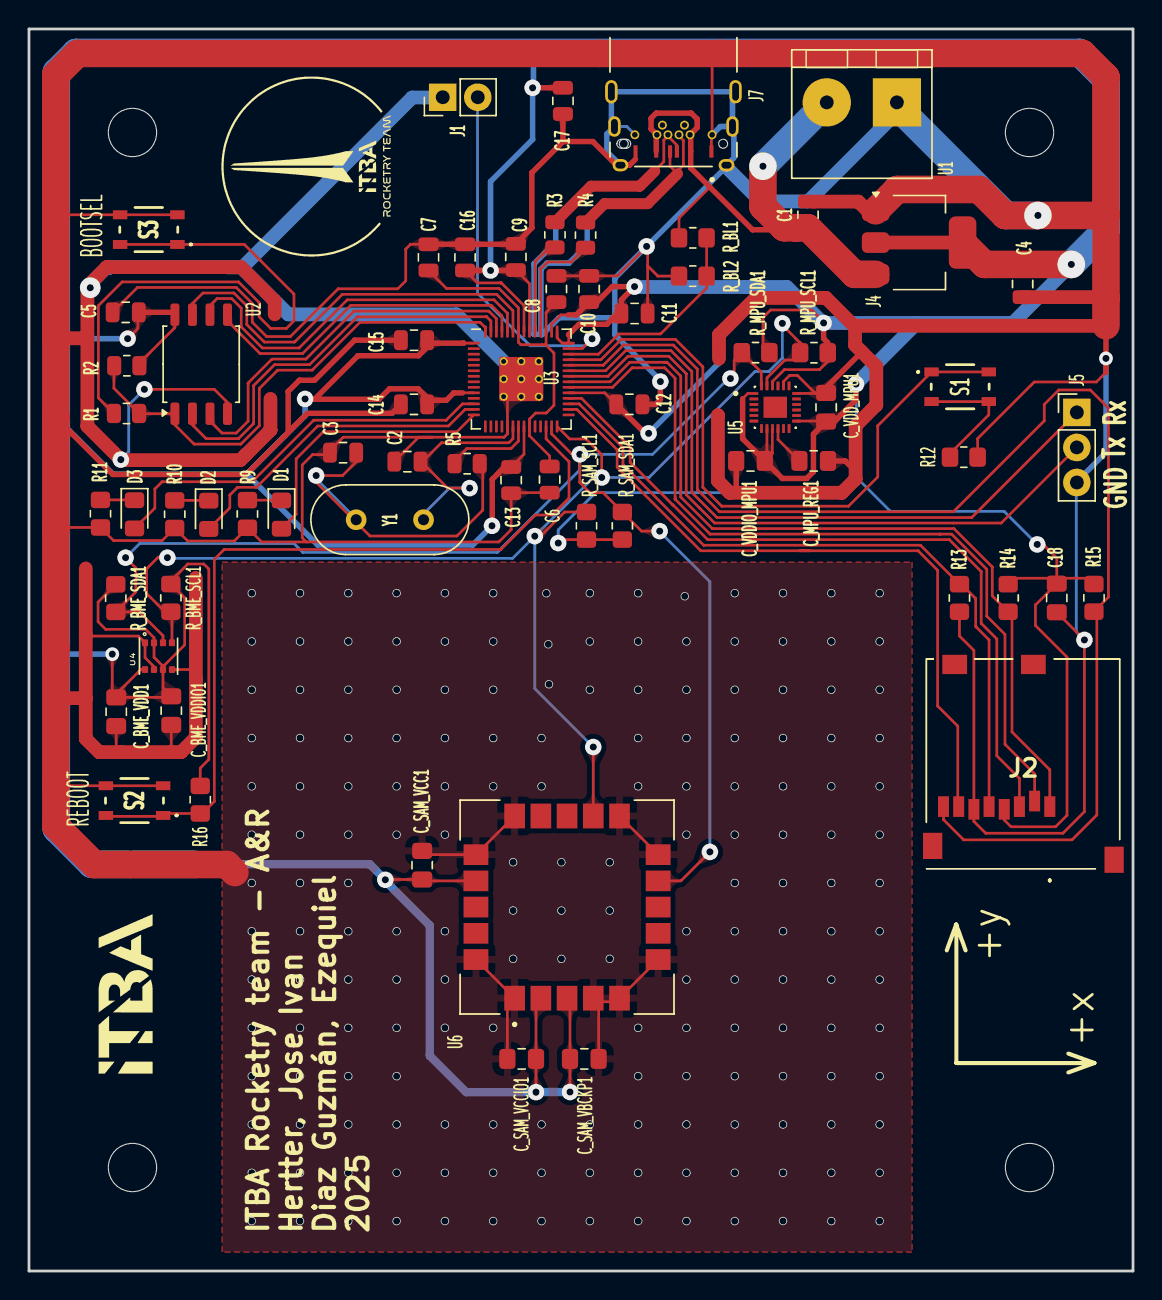
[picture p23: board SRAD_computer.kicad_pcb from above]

Board: 2 copper layers, 80.0 x 90.0 mm, 69 parts (0 on the bottom side), 40 nets.

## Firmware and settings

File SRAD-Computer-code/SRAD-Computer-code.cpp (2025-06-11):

#include "SRAD-Computer-code.h"

XBee xbee(uart_cfg, to_ms_since_boot(get_absolute_time()));

flash_global_vars_t global_vars = {0};

packet parameters = {PRE_LAUNCH, 0};

int main()
{

    parameters.status = PRE_LAUNCH;
    stdio_init_all();
    init_leds();

    // Init airbrake&payload pin
    gpio_init(PIN_AIRBRAKE);
    gpio_set_dir(PIN_AIRBRAKE, GPIO_OUT);
    gpio_put(PIN_AIRBRAKE, 0);

    // Initialize I2C Bus
    gpio_init(PIN_I2C_SCL);
    gpio_init(PIN_I2C_SDA);
    i2c_init(&i2c_setUp, I2C_FREQUENCY); // 320kHz
    gpio_set_function(PIN_I2C_SDA, GPIO_FUNC_I2C);
    gpio_set_function(PIN_I2C_SCL, GPIO_FUNC_I2C);
    gpio_pull_up(PIN_I2C_SDA);
    gpio_pull_up(PIN_I2C_SCL);

    gpio_set_function(PIN_UART_TX, GPIO_FUNC_UART);
    gpio_set_function(PIN_UART_RX, GPIO_FUNC_UART);

    // Initialize ADC for battery voltage measurement
    adc_init();
    adc_gpio_init(PIN_ADC_BATTERY); // ADC0
    adc_select_input(PIN_ADC_BATTERY); // Select ADC0 (GPIO26) for battery voltage measurement

    // Set global variables as they were on last boot (just in case SRAD resets middle flight)
    // flashReadGlobalData();

    // Initialize ICM-20948
    if (icm20948_init(&IMU_config) != 0)
    {
        printf("IMU not detected at I2C address. Freezing");
        error_led();
        while (true)
            ;
    }
    gpio_toggle(PIN_LED_ALTITUDE);

    data.accel_bias[0] = accel_bias[0];
    data.accel_bias[1] = accel_bias[1];
    data.accel_bias[2] = accel_bias[2];

    // Initialize BME280
    if (BME.begin(0x76, 0x60) == false)
    {
        printf("BME not detected at default I2C address. Freezing.");
        error_led();
        while (1)
            ;
    }

    gpio_toggle(PIN_LED_ON);

    // Initialize SAM_M8Q
    if (GNSS.begin(i2c_setUp, 0x42) == false) // Connect to the Ublox module using Wire port
    {
        printf("GNSS not detected at default I2C address. Freezing.");
        error_led();
        while (1)
            ;
    }
    else
    {
        sleep_ms(200);
        GNSS.enableGNSS(true, SFE_UBLOX_GNSS_ID_GPS);
        sleep_ms(200);
        GNSS.enableGNSS(false, SFE_UBLOX_GNSS_ID_GLONASS);
        sleep_ms(200);
        GNSS.setNavigationFrequency(20);
        sleep_ms(200);
        GNSS.setAutoPVTrate(20);
        sleep_ms(200);
        GNSS.setHNRNavigationRate(15);
        sleep_ms(200);

        gpio_put(PIN_LED_ERROR, 1);

#if NDEBUG_SAT
        if(parameters.status == PRE_LAUNCH)
        {
            do {
                parameters.satellite_count = GNSS.getSIV();
                printf("Waiting for GNSS satellites: %d\n", parameters.satellite_count);
            } while (parameters.satellite_count < 1);
        }
#endif
    }
    init_leds();

    gpio_put(PIN_LED_ON, 1);

    while (true)
    {
        // static uint32_t last_time = 0;

        // if (to_ms_since_boot(get_absolute_time()) - last_time > 5) // 200Hz
        // {
        //     last_time = to_ms_since_boot(get_absolute_time());
        //     readData();
        //     telemetry();
        // }

        switch (parameters.status)
        {
        case PRE_LAUNCH:
            waitForStart();
            break;
        case LAUNCH:
            waitForLaunch();
            break;
        case ASCENT:
            ascentRoutine();
            break;
        case APOGEE:
            apogeeRoutine();
            break;
        case DESCENT:
            descentRoutine();
            break;
        // case LANDING:
        //     break;
        case RECOVERY:
            recoverySignal();
            break;
        }
    }
}

void gpio_toggle(int pin)
{
    if (gpio_get(pin))
        gpio_put(pin, 0);
    else
        gpio_put(pin, 1);
}

void error_led()
{
    gpio_put(PIN_LED_ERROR, 1);
    gpio_put(PIN_LED_ALTITUDE, 0);
    gpio_put(PIN_LED_ON, 0);
}

void updateXbeeParameters(uint32_t last_time)
{
    static bool si = true;
    // Mission data
    xbee.setMissionTime(last_time);
    xbee.setPacketCount();
    xbee.setStatus(parameters.status);
    parameters.battery_level = (uint8_t)(adc_read() * 9.336f / 4096.0f * 100); // Convert ADC value to percentage
    xbee.setBatteryVoltage(parameters.battery_level);
    
    // IMU data
    xbee.setIMUVerticalVel(parameters.imu_vel_y);
    xbee.setIMURoll(parameters.imu_roll);
    xbee.setIMUPitch(parameters.imu_pitch);
    
    // GNSS data
    xbee.setGNSSTime(parameters.gnss_time);
    xbee.setGNSSLatitude(parameters.gnss_latitude);
    xbee.setGNSSLongitude(parameters.gnss_longitude);
    xbee.setGNSSAltitude(parameters.gnss_altitude, parameters.gnss_altitude_MSL);
    
    // ESU data
    xbee.setBMEPressure(parameters.bme_pressure);
    xbee.setBMEAltitude(parameters.bme_altitude);
    xbee.setBMETemperature(parameters.bme_temperature);
}

void readData()
{
    static uint8_t times = 0;
    readIMU();

    if ((times % 5) == 0)
        readBME();

    if ((times % 20) == 0)
        readGNSS();

    times++;
    if (times > 240)
        times = 0;
}

void readIMU()
{
    static float accel_g[3] = {0};
    static float gyro_dps[3] = {0};

    icm20948_read_cal_accel(&IMU_config, &data.accel_raw[0], &data.accel_bias[0]);
    icm20948_read_cal_gyro(&IMU_config, &data.gyro_raw[0], &data.gyro_bias[0]);

    accel_g[0] = (float)data.accel_raw[0] / 4096.0f;
    accel_g[1] = (float)data.accel_raw[1] / 4096.0f;
    accel_g[2] = (float)data.accel_raw[2] / 4096.0f;

    gyro_dps[0] = (float)data.gyro_raw[0] / 131.0f;
    gyro_dps[1] = (float)data.gyro_raw[1] / 131.0f;

    parameters.imu_roll = (int16_t)(atan2(-accel_g[0], accel_g[2]) * RAD_TO_DEG * 10);
    parameters.imu_pitch = (int16_t)(atan(accel_g[1] / sqrt(accel_g[0] * accel_g[0] + accel_g[2] * accel_g[2])) * RAD_TO_DEG * 10);

    parameters.imu_accel_y = (accel_g[1] * (-GRAVITY));                                                                   // m/s^2
    parameters.imu_accel_y = (ABS(parameters.imu_accel_y) < STATIC_ACCELEROMETER_THRESHOLD) ? 0 : parameters.imu_accel_y; // m/s^2

    calculateIMUvelocity(accel_g[1], gyro_dps[1]);
}

/**
 * @brief Integrates Acceleration to obtain velicty with ZUPT correction.
 *
 * @param accel_g_y
 * @param gyro_dps_y
 */
void calculateIMUvelocity(float accel_g_y, float gyro_dps_y)
{
    static float prev_accel_y = 0; // in graviy units
    static float delta_vel_y = 0;  // in m/s

    static float vel_y = 0;

    // ZUPT -> Zero Velocitu Update
    if ((ABS(accel_g_y - 1) < STATIC_ACCELEROMETER_THRESHOLD) && (ABS(gyro_dps_y) < STATIC_GYROSCOPE_THRESHOLD))
        delta_vel_y = 0;
    else
        delta_vel_y = 0.5 * (accel_g_y + prev_accel_y) * GRAVITY * IMU_SAMPLING_PERIOD;

    vel_y += delta_vel_y; // m/s
    prev_accel_y = accel_g_y;

    parameters.imu_vel_y = (int32_t)(vel_y * 100);
}

void readGNSS()
{
    // static bool first_time = true;

    // if (first_time)
    // {
    parameters.satellite_count = GNSS.getSIV();

    //     if (parameters.satellite_count > 20)
    //         parameters.satellite_count = 0;

    //     if (parameters.satellite_count > 0)
    //         first_time = false;
    // }

    // This is fot the velocity calculation, just for comparison with the IMU velocity
    static int32_t last_altitude = 0;
    static uint32_t period = to_ms_since_boot(get_absolute_time())/1000; 

#if NDEBUG_SAT
    if (parameters.satellite_count > 0)
    {
        period = to_ms_since_boot(get_absolute_time()) / 1000 - period; // seconds
        last_altitude = parameters.gnss_altitude;

        parameters.gnss_time = (uint32_t)(GNSS.getHour() * 10000 + GNSS.getMinute() * 100 + GNSS.getSecond());
        parameters.gnss_latitude = GNSS.getLatitude();   // latitude +-90ª
        parameters.gnss_longitude = GNSS.getLongitude(); // longitude +-180ª
        parameters.gnss_altitude = (GNSS.getAltitude() - altitude_bias) / 1000;
        // parameters.gnss_altitude = GNSS.getAltitudeMSL();
    
        parameters.gnss_velocity = (parameters.gnss_altitude - last_altitude) / period; // m/s
    }
#else
    // dummy parameters for testing
    parameters.satellite_count = 10; // GNSS.getSIV();
    parameters.gnss_time = 123456; // GNSS.getHour() * 10000 + GNSS.getMinute() * 100 + GNSS.getSecond();
    parameters.gnss_latitude = 0;   // GNSS.getLatitude();   // latitude +-90ª
    parameters.gnss_longitude = 0; // GNSS.getLongitude(); // longitude +-180ª
    parameters.gnss_altitude = 0; // (GNSS.getAltitude() - altitude_bias) / 1000;
#endif
}

// Returns the current pressure. Handy to have for calibration processes
void calibrateBME(void)
{
    float pressure = BME.readPressure();
    pressure /= 100;
    ground_hP = pressure;
}

void readBME()
{
    parameters.bme_temperature = (int32_t)(BME.readTemperature() * 100);
    parameters.bme_pressure = (uint32_t)BME.readPressure();
    parameters.bme_altitude = (int32_t)BME.readAltitude(1013.25f); 
}

void init_leds()
{
    for (int i = 0; i < gpio_size; i++)
    {
        gpio_init(gpio_array[i]);
        gpio_set_dir(gpio_array[i], GPIO_OUT);
        gpio_put(gpio_array[i], 0);
    }

    for (int i = 0; i < 6; i++)
    {
        gpio_toggle(PIN_LED_ALTITUDE);
        sleep_ms(100);
        gpio_toggle(PIN_LED_ERROR);
        sleep_ms(100);
        gpio_toggle(PIN_LED_ON);
        sleep_ms(100);
    }
}

/*
Función que guarda estructuras en un buffer, y cuando este se llena, guarda este
buffer en memoria flash.
Recibe: La estructura con los datos actuales del sistema (Posición, altura, etc)
Devuelve: La cantidad de veces que se escribió un sector en memoria

Si se quedó sin memoria, va a devolver siempre la misma cantidad de veces que se
guardó en el buffer la estructura, pero no se va a poder guardar más información.
En este caso, todo lo que esté en el buffer, se va a perder si se apaga el sistema.
*/
uint32_t flashSaveData(packet data)
{
    static uint8_t buff_count = 0;
    static uint32_t saves = 0;
    static bool out_of_memory = false;

    if (buff_count < BUFFER_SIZE)
    {
        buffer_flash[buff_count] = data;
        buff_count++;
    }
    else if (!out_of_memory) // Si el buffer se llenó y no se quedó sin memoria
    {
        // La idea es borrar los sectores a medida que necesitemos. Entran 16 páginas
        //(escrituras), por lo que cada 16 iteraciones borramos el siguiente sector
        if (saves % 16 == 0)
        {
            uint32_t erase_addr = (FLASH_SIZE) - (uint32_t)(FLASH_SECTOR_SIZE * ((uint32_t)(saves / 16) + 2)); //+2 para reservar el último para las variables globales
            if (erase_addr <= FLASH_CODE_END)                                                        // No borrar el sector de código
            {
                out_of_memory = true;
                return saves;
            }

            uint32_t ints = save_and_disable_interrupts();
            flash_range_erase(erase_addr, FLASH_SECTOR_SIZE);
            restore_interrupts(ints);
        }
        // Después de borrar (si fue necesario), guardamos el buffer en memoria
        uint32_t prog_addr = (FLASH_SIZE)-(FLASH_SECTOR_SIZE) - (FLASH_PAGE_SIZE * (saves+1)); // notar que el ultimo sector es para las variables globales

        uint32_t ints = save_and_disable_interrupts();
        flash_range_program(prog_addr, (uint8_t *)(buffer_flash), FLASH_PAGE_SIZE);
        restore_interrupts(ints);

        saves++;
        buff_count = 0;
    }
    return saves;
}

void flashRead(uint32_t n_pages)
{
    static packet *data_ptr = (packet *)(XIP_BASE + (FLASH_SIZE) - FLASH_SECTOR_SIZE -FLASH_PAGE_SIZE);

    for (uint32_t j = 0; j < n_pages; j++)
    {
        for (uint8_t i = 0; i < BUFFER_SIZE; i++) // este for mandaría todas las estructuras, una por una, por el puerto serie
        {
            for (uint8_t k = 0; k < sizeof(packet); k++) // este for mandaría todos los bytes de la estructura, uno por uno, por el puerto serie
            {
                printf("%02X", data_ptr[j]);
            }
            printf("\n");
            data_ptr++;
        }
        data_ptr = (packet *)(XIP_BASE + (FLASH_SIZE) - FLASH_SECTOR_SIZE - (FLASH_PAGE_SIZE * (j + 2)));
    }
}

void flashSaveGlobalData(flash_global_vars_t data)
{
    buffer_global[0] = global_vars;
    uint32_t erase_addr = (FLASH_SIZE) - (FLASH_SECTOR_SIZE);
    uint32_t prog_addr = (FLASH_SIZE) - (FLASH_PAGE_SIZE * 2); // No guardamos en la última página para dejar lugar a futuras implementaciones y tests
    uint32_t ints = save_and_disable_interrupts();
    flash_range_erase(erase_addr, FLASH_SECTOR_SIZE);
    restore_interrupts(ints);

    ints = save_and_disable_interrupts();
    flash_range_program(prog_addr, (uint8_t *)&buffer_global, FLASH_PAGE_SIZE);
    restore_interrupts(ints);
}

void flashReadGlobalData(void)
{
    static flash_global_vars_t *flash_variables = (flash_global_vars_t *)(XIP_BASE + (FLASH_SIZE) - (FLASH_PAGE_SIZE * 2));
    global_vars = *flash_variables;
}

void flashResetGlobalData(void)
{
    static const uint32_t erase_addr = (FLASH_SIZE) - (FLASH_SECTOR_SIZE);
    uint32_t ints = save_and_disable_interrupts();
    flash_range_erase(erase_addr, FLASH_SECTOR_SIZE);
    restore_interrupts(ints);
}

bool checkAccel(void)
{
    // if (parameters.imu_accel_y > 0)
    //     return true;
    // else
    //     return false;

    return false;
}

/**
 * @brief   Waits for START signal from ground station. Sends ACK.
 *          If no signal is received, double checks vertical acceleration.
 *
 */
void waitForStart(void)
{
    // leemos uart hasta que llegue el char de inicio (START)
    //  Manda ACK
    // si nunca llega START y empieza a acelerar el weon, pasamos a estado LAUNCH
    static uint32_t last_time = 0;

    if (xbee.receiveStartSignal() || parameters.imu_accel_y > 0)
    // if (xbee.receiveStartSignal())
    {
        gpio_put(PIN_LED_ON, 1);
        // printf("START signal received.\n");
        calibrateRocket();
        parameters.status = LAUNCH;
        global_vars.last_status = parameters.status;
        // flashSaveGlobalData(global_vars); // Guardado de parámetros globales en flash
        return;
    }

    if (to_ms_since_boot(get_absolute_time()) - last_time > 1000) // para leer aceleración vertical, por si no llega el START
    {
        last_time = to_ms_since_boot(get_absolute_time()); // Update the timer
        gpio_toggle(PIN_LED_ON);
        readData();
        telemetry();
    }
}

/**
 * @brief   Calibrate rocket parameters (GNSS altitude,
 *          pressure sensor offset & imu bias) and
 *          starts payload.
 *
 */
void calibrateRocket(void)
{
    // Y manda el telegrama a la payload con el pin que va a la ESP32
    // ASEGURARSE QUE VAN A PASAR X SEGUNDOS PARA QUE SE PRENDA LA PAYLOAD
    // dejamos de leer UART, seteamos el puerto para sólo enviarle chars

    icm20948_cal_gyro(&IMU_config, &data.gyro_bias[0]);
    calibrateBME();                     // Actualizamos la presión actual en el suelo, así calculamos la altura a partir de esto
    altitude_bias = GNSS.getAltitude(); // :+1:
    global_vars.initial_lat = GNSS.getLatitude();
    global_vars.initial_long = GNSS.getLongitude();
    airbrake_payload(true);
}

/**
 * @brief NOP unless accel > 0
 *
 */
void waitForLaunch(void)
{
    static uint32_t last_time = 0, tel_time =0;

    // Change mission status
    if (parameters.imu_accel_y > 0)
    {
        parameters.status = ASCENT;
        global_vars.last_status = ASCENT;
        // flashSaveGlobalData(global_vars); // Guardado de parámetros globales en flash
        gpio_put(PIN_LED_ON, 1);
        return;
    }
    
    // Telemetry
    if (to_ms_since_boot(get_absolute_time()) - tel_time > 250)
    {
        gpio_toggle(PIN_LED_ON);

        // @twickham: Test if error is on line below
        tel_time = to_ms_since_boot(get_absolute_time()); // Update the timer
        telemetry();
    }

    // Save Data
    if (to_ms_since_boot(get_absolute_time()) - last_time > 5)
    {
        last_time = to_ms_since_boot(get_absolute_time()); // Update the timer

        readData();
        global_vars.cant_pages = flashSaveData(parameters);
    }
    
    return;
}

void ascentRoutine(void)
{
    static uint32_t last_time = 0;

    if (parameters.gnss_altitude > AIRBRAKE_HEIGHT)
    {
        parameters.status = APOGEE;
        global_vars.last_status = APOGEE;
        // flashSaveGlobalData(global_vars); // Guardado de parámetros globales en flash
        gpio_put(PIN_AIRBRAKE, 0); // Open airbrake
        return;
    }

    if (to_ms_since_boot(get_absolute_time()) - last_time > 5)
    {
        last_time = to_ms_since_boot(get_absolute_time()); // Update the timer

        readData();

        global_vars.cant_pages = flashSaveData(parameters); // guardado de datos actuales en flash
    }

    telemetry();

    return;
}

/**
 * @brief Transmits telemetry through xbee
 *
 */
void telemetry(void)
{
    static uint32_t last_time_xbee = 0;

    if (to_ms_since_boot(get_absolute_time()) - last_time_xbee > 100)
    {
        last_time_xbee = to_ms_since_boot(get_absolute_time());
        updateXbeeParameters(last_time_xbee);
        xbee.sendPkt();

#if PRINT_DEBUG_PKT

        printf("%d - ", parameters.satellite_count);

        xbee.sendParameter(MISSION_TIME);
        xbee.sendParameter(PACKET_COUNT);
        xbee.sendParameter(MISSION_STATUS);
        xbee.sendParameter(BATTERY_LEVEL);

        printf("- ");

        xbee.sendParameter(IMU_ROLL);
        xbee.sendParameter(IMU_PITCH);
        xbee.sendParameter(IMU_Y_VEL);

        printf("- ");

        if (parameters.satellite_count > 0)
        {
            xbee.sendParameter(GNSS_TIME);
            xbee.sendParameter(GNSS_LATITUDE);
            xbee.sendParameter(GNSS_LONGITUDE);
            xbee.sendParameter(GNSS_ALTITUDE);
        }

        printf("- ");

        xbee.sendParameter(BME_PRESSURE);
        xbee.sendParameter(BME_ALTITUDE);
        xbee.sendParameter(BME_TEMPERATURE);

        printf("\n");
#endif
    }
}

/**
 * @brief 	When 2000m are reached, starts airbrake control.
 * 			Stores max height.
 *
 */
void apogeeRoutine(void)
{
    static uint32_t last_time = 0;
    static int32_t altitude_memory[5] = {0};
    static bool descent_flag = false;

    // if (parameters.imu_vel_y < 0) // hasta que no funcione del todo bien la velocidad, calcular altura
    if (descent_flag)
    {
        gpio_put(PIN_AIRBRAKE, 1); // Close airbrake
        parameters.status = DESCENT;
        global_vars.last_status = DESCENT;
        global_vars.max_altitude = altitude_memory[0]; 
        // flashSaveGlobalData(global_vars); // Guardado de parámetros globales en flash
        return;
    }

    if (to_ms_since_boot(get_absolute_time()) - last_time > 5)
    {
        last_time = to_ms_since_boot(get_absolute_time()); // Update the timer

        readData();
        global_vars.cant_pages = flashSaveData(parameters); // Guardado de datos actuales en flash
        // airbrake_payload();
 
        for (int i = 0; i < 4; i++)
        {
            altitude_memory[i] = altitude_memory[i + 1]; // Shift the array
        }
        altitude_memory[4] = parameters.gnss_altitude; // Add the current altitude

        for (int i = 1; i < 5; i++)
        {
            if (altitude_memory[i] > altitude_memory[0])
                break;

            if (i == 4) // Apogee was reached, we are descending
                descent_flag = true;
        }

    }
    telemetry();
}

void descentRoutine(void)
{
    static uint32_t last_time = 0;

    if (((parameters.gnss_altitude < 100) && (parameters.imu_vel_y > -2 && parameters.imu_vel_y < 2)) || parameters.gnss_altitude < 5) // Si está descendiendo lo suficientemente lento como para decir que aterrizó
    {
        parameters.status = RECOVERY;
        global_vars.last_status = RECOVERY;
        // flashSaveGlobalData(global_vars); // Guardado de parámetros globales en flash
        return;
    }

    if (to_ms_since_boot(get_absolute_time()) - last_time > 5)
    {
        last_time = to_ms_since_boot(get_absolute_time()); // Update the timer

        readData();                                    // :+1:
        global_vars.cant_pages = flashSaveData(parameters); // Guardado de datos actuales en flash
    }
    telemetry();
}

/**
 * @brief 	Sends absolute coordinates and time to GS.
 * 			Starts max altitude protocol.
 *
 */
void recoverySignal(void)
{
    static uint32_t last_time = 0;

    if (to_ms_since_boot(get_absolute_time()) - last_time > 5000)
    {
        last_time = to_ms_since_boot(get_absolute_time()); // Update the timer
        telemetry();
    }
}

/**
 * @brief 	Shuts down sensors -> enters low energy mode.
 *
 */
void standByMode(void)
{
    // TODO: Si la bateria no llegase a alcanzar, apagar todos los sensores
}

/**
 * @brief   PIN_AIRBRAKE = 1 : airbrake closed
 *          PIN_AIRBRAKE = 0 : airbrake open
 *
 * @param payload
 */
void airbrake_payload(bool payload)
{
    static bool pin_state = false;
    static int16_t poly_curve_1 = 0;
    static int16_t poly_curve_3 = 0;

    pin_state = gpio_get(PIN_AIRBRAKE);
    poly_curve_1 = (int16_t)(-1.209e-7 * (float)pow(parameters.imu_vel_y, 4) + 1.479e-4 * pow(parameters.imu_vel_y, 3) - 5.82e-2 * pow(parameters.imu_vel_y, 2) + 3053);
    poly_curve_3 = (int16_t)(1.088e-7 * (float)pow(parameters.imu_vel_y, 4) + 3.179e-5 * pow(parameters.imu_vel_y, 3) - 5.009e-2 * pow(parameters.imu_vel_y, 2) + 3047);

    if (payload)
        gpio_put(PIN_AIRBRAKE, 1);
    else
    {
        if ((parameters.gnss_altitude > poly_curve_3) && pin_state)
            gpio_put(PIN_AIRBRAKE, 0); // Open airprake
        else if ((parameters.gnss_altitude < poly_curve_1) && !pin_state)
            gpio_put(PIN_AIRBRAKE, 1); // Close airbrake
    }
}

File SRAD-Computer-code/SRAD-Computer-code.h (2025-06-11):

#ifndef SRAD_computer 
#define SRAD_computer

#include <stdio.h>
#include "pico/stdlib.h"
#include "pico/time.h"
#include "hardware/i2c.h"
#include "hardware/gpio.h"
#include "hardware/flash.h" //para programar y borrar flash
#include "hardware/sync.h"  //para interrupciones
#include "hardware/adc.h"

#include "libraries/icm_20948/pico-icm20948.h"
#include "libraries/MadgwickAHRS/MadgwickAHRS.h"
#include "libraries/sam_m8q_v2/sam_m8q_v2.h"
#include "libraries/bmp_280/bmp280.h"
#include "libraries/XBee/XBee.h"

#define NDEBUG_SAT          1
#define PRINT_DEBUG_PKT     0

#define I2C_FREQUENCY       400000

#define PIN_LED_ON          11
#define PIN_LED_ERROR       10
#define PIN_LED_ALTITUDE    9

#define PIN_I2C_SDA         16
#define PIN_I2C_SCL         17

#define PIN_AIRBRAKE        29
#define PIN_ADC_BATTERY     28

#define UART_ID             uart1
#define UART_BAUD           115200
#define UART_STOP_BITS      1
#define UART_DATA_BITS      8
#define UART_PARITY         UART_PARITY_NONE

#define FLASH_OFFSET        (0x01000000) // definimos un offset para no pisar nuestro código
#define FLASH_CODE_END      ((uint32_t)(XIP_BASE + FLASH_OFFSET)) //Hardcodear cuando tengamos el código final

#define AIRBRAKE_HEIGHT     2000    // Height in meters

#define ABS(x)              ((x) < 0 ? -(x) : (x))
#define RAD_TO_DEG          (180.0f / 3.14159265358979323846f)
#define DEG_TO_RAD          (1 / RAD_TO_DEG)
#define GRAVITY             (9.80665f)
#define IMU_SAMPLING_RATE   (200.0f)                     // Hz
#define IMU_SAMPLING_PERIOD (1.0f / IMU_SAMPLING_RATE) // seconds
#define STATIC_ACCELEROMETER_THRESHOLD (0.12f)         // m/s^2
#define STATIC_GYROSCOPE_THRESHOLD (3.0f)              // m/s

const int gpio_size = 3;
const int gpio_array[] = {
    PIN_LED_ON,
    PIN_LED_ALTITUDE,
    PIN_LED_ERROR};

const int16_t accel_bias [3] = {96, -94, 5};
int16_t altitude_bias = 0;

i2c_inst_t i2c_setUp = {i2c0_hw, false};
icm20948_config_t IMU_config = {0x69, 0x0C, &i2c_setUp};
icm20984_data_t data;
madgwick_ahrs_t filter = {0.5f, {1.0f, 0.0f, 0.0f, 0.0f}};
BMP280 BME(&i2c_setUp);
SFE_UBLOX_GNSS GNSS;


xbee_uart_cfg_t uart_cfg = {UART_ID, UART_BAUD, UART_STOP_BITS, UART_DATA_BITS, UART_PARITY};

const uint8_t *flashBase = (const uint8_t *)(XIP_BASE + FLASH_OFFSET);

typedef struct
{
    uint32_t status;
    uint32_t battery_level = 0;

    uint32_t bme_pressure = 0;
    int32_t bme_temperature = 0;
    int32_t bme_altitude = 0;

    uint8_t satellite_count = 0;
    uint32_t gnss_time = 0;
    int32_t gnss_latitude = 0;  // latitude +-90ª
    int32_t gnss_longitude = 0; // longitude +-180ª
    int32_t gnss_altitude = 0;
    int32_t gnss_altitude_MSL = 0;
    int32_t gnss_velocity = 0;

    int32_t imu_roll = 0;
    int32_t imu_pitch = 0;
    int32_t imu_vel_y = 0;  // cm/s
    int32_t imu_accel_y = 0; // cm/s^2
} packet;

typedef struct {
    uint8_t last_status;
    int32_t initial_lat;
    int32_t initial_long;
    int32_t final_lat;
    int32_t final_long;
    uint32_t mission_duration;
    int16_t max_altitude;
    uint32_t cant_pages;
} flash_global_vars_t;

// typedef enum {
// 	RESET_MISSION = 0,
// 	MOVE,
// 	STAY,
// } fsm_actions_t;

#define BUFFER_SIZE ((uint8_t)(FLASH_PAGE_SIZE / sizeof(packet)))
#define FLASH_SIZE ((uint32_t)(16 * 1024 * 1024))

void readData();
void updateXbeeParameters(uint32_t last_time);

void readIMU();
void readGNSS();
void readBME();
void calibrateBME(void);
static float ground_hP = 0;

void gpio_toggle(int pin);
void init_leds();
void error_led(void);

packet buffer_flash[BUFFER_SIZE];
flash_global_vars_t buffer_global [((uint8_t)(FLASH_PAGE_SIZE / sizeof(flash_global_vars_t)))];
uint32_t flashSaveData(packet data);
void flashRead(uint32_t n_pages);
void flashSaveGlobalData(flash_global_vars_t data);
void flashReadGlobalData(void);
void flashResetGlobalData(void);
/*******************
 *  State machine
 *******************/
void waitForStart(void);
void calibrateRocket(void);
void waitForLaunch(void);
void telemetry(void);
void ascentRoutine(void);
void apogeeRoutine(void);
void descentRoutine(void);
void recoverySignal(void);
void standByMode(void); 
void airbrake_payload(bool payload = false);
void calculateIMUvelocity(float accel_g_y, float gyro_dps_y);

#endif 

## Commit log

2025-03-11 creación proyecto kicad
    [SRAD_computer.kicad_pcb, SRAD_computer.kicad_sch]
2025-03-11 RP2040 minimal components placed
    [SRAD_computer.kicad_pcb, SRAD_computer.kicad_sch]
2025-03-17 schematic update: MPU, BME & SAM m8q
    [SRAD_computer.kicad_sch]
2025-03-18 PCB placement
    [SRAD_computer.kicad_pcb]
2025-03-19 RP2040 decoupling capacitors and resistances connection
    [SRAD_computer.kicad_pcb, SRAD_computer.kicad_sch]
2025-03-21 update PCB
    [SRAD_computer.kicad_pcb, SRAD_computer.kicad_sch]
2025-03-21 PCB Update
    [SRAD_computer.kicad_pcb]
2025-03-27 Change Layout: Shield for GPS
    [SRAD_computer.kicad_pcb]
2025-03-27 Changed board size & GPS shielding
    [SRAD_computer.kicad_pcb]
2025-03-28 Update PCB placement & 3D models added
    [BME280.step, MPU-9250.step, RP2040_QFN_PACKAGE.STEP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]
2025-03-28 PCB v1
    [0805_res.step, SRAD_computer.kicad_pcb, SRAD_computer.kicad_sch]
2025-03-31 SD slot, LEDs and switch added
    [Crystal_HC49-4H.step, PTS810SJK250SMTR_LFS.step, SRAD_computer.csv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]
2025-04-01 PCB_V1 finished
    [SRAD_computer.csv, SRAD_computer.kicad_pcb]
2025-04-01 PCB 3D model added
    [SRAD_computer.kicad_pcb, SRAD_computer.kicad_sch]
2025-04-04 PCB V2 first draft
    [SRAD_computer.csv, SRAD_computer.kicad_pcb, SRAD_computer.kicad_sch]
2025-04-06 changes in USB pins. D+ -> D-
    [SRAD_computer.kicad_pcb, SRAD_computer.kicad_sch]
2025-04-06 USB gnd fixed
    [SRAD_computer.kicad_pcb]
2025-04-07 SD layout
    [SRAD_computer.kicad_pcb, SRAD_computer.kicad_sch]
2025-04-08 USB footprint changed & reboot sw added
    [SRAD_computer.kicad_pcb, SRAD_computer.kicad_sch]
2025-04-08 GPS ground plane fixed
    [SRAD_computer.kicad_pcb]
2025-04-09 reboot and bootsel buttons added
    [SRAD_computer-B_Cu.gbr, SRAD_computer-B_Mask.gbr, SRAD_computer-B_Paste.gbr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]
2025-04-09 Reading data from IMU: Done
2025-04-10 Work in progress: migrate arduino libraries to rpi
2025-04-11 Migration Failed - Reimagining M8Q driver
    [SRAD-Computer-code.cpp]
2025-04-11 Pin for battery level added
    [SRAD_computer.kicad_pcb, SRAD_computer.kicad_sch]
2025-04-14 m8q does not respond - ERROR 404
    [SRAD-Computer-code.cpp]
2025-04-14 Gerber files added
    [SRAD_computer-B_Cu.gbl, SRAD_computer-B_Mask.gbs, SRAD_computer-B_Paste.gbp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]
2025-04-14 changed SD socket & updated gerber files
    [503398-1892.step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]
2025-04-14 Better 3D model created
    [SRAD_computer.FCStd]
2025-04-14 Rearranged some files
    [SRAD_computer-B_Cu.gbl, SRAD_computer-B_Mask.gbs, SRAD_computer-B_Paste.gbp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]
2025-04-14 Changed micro SD socket footprint
    [SRAD_computer-B_Cu.gbl, SRAD_computer-B_Mask.gbs, SRAD_computer-B_Paste.gbp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]
2025-05-02 XBee class added: parser in progress & mission time; ESU driver added: not working
    [SRAD-Computer-code.cpp]
2025-05-06 reorganized directory
    [0805_res.step, 503398-1892.step, BME280.step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]
2025-05-12 IMU fixed
    [SRAD_computer.kicad_pcb, SRAD_computer.kicad_sch]
2025-05-13 XBee: pitch & roll work fine; Still troubleshooting velocity
2025-05-13 Updated PCB: some UART pin errors & missing conection on icm
    [SRAD_computer.kicad_pcb, SRAD_computer.kicad_sch]
2025-05-13 velocity testing: firsts approach
2025-05-14 ZUPT: simple zero velocity update algorithm added to mitigate velofity drift
    [SRAD-Computer-code.cpp]
2025-05-22 issue setting navigation rate: sendCommand does not ACK
    [SRAD-Computer-code.cpp, SRAD-Computer-code.h]
2025-05-22 SAM M8Q library bug found, ready for testing
    [SRAD-Computer-code.cpp]
2025-05-22 GNSS transmission rate fixed
    [SRAD-Computer-code.cpp, SRAD-Computer-code.h]
2025-05-23 Velocity testbench: extracted data from past editions
    [altitude_flight_data.csv, apogee.csv, velocity_flight_data.csv]
2025-05-23 FSM was replaced with a simpler version
    [SRAD-Computer-code.cpp, SRAD-Computer-code.h]
2025-05-23 Airbrake function
    [SRAD_computer.kicad_pcb, SRAD_computer.kicad_sch]
2025-05-24 v1 SRAD computer finished: test remaining
    [altitude_flight_data.csv, processed_flight_data.csv, raw_altitude_flight_data.csv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]
2025-05-30 parser error & bme altitude fixed; test bench data ready
    [SRAD-Computer-code.cpp, SRAD-Computer-code.h, velocity_test.py]
2025-05-30 uart_getc problem
2025-06-04 fsm tested
    [BOM.csv, SRAD_computer.kicad_sch]
2025-06-10 LED_ON turns on on ASCENT
2025-06-11 Comentado de guardados globales en la flash. Los guardados frecuentes se siguen haciendo
